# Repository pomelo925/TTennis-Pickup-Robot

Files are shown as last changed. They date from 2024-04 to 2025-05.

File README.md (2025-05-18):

<div align="center">
 <h1> TTennis Pickup Robot 桌球自動拾取智慧機器人 </h1>
</div>

> 清華大學 動力機械系25級 畢業專題（2024）

> 本人（pomelo925）負責項目為全軟體、部分韌體及部分電路。
> 非本人負責項目最終會清楚標註貢獻者。

TTennis Pickup Robot 目標是在任意的桌球場中，自動化完成拾取，並抬升內置球架供運動員使用或將桌球傾倒於球架中，使選手能專注於訓練本身。TTennis Pickup Robot 具備動態避障能力，同時用戶可透過遙控器或螢幕來操控機器人，並調整機器人運動參數。

TTennis Pickup Robot 從機構設計、電路板設計、單晶片調適至上層的視覺處理、AI 模型部署、建圖定位與導航避障系統等皆是我們針對特殊的應用場景做開發，並不直接使用市面上的套件。同時軟韌體算法全部開源，代碼已解藕封裝，所有運行節點以虛擬化容器形式運行，十分利於有程式背景的人對特定算法做二次開發。

<br/>


<center>
<p> 以 Nextjs / Framer Motion / Tailwind CSS 製作的 Web 操控介面。 <p>
</center>

</br>

<div align="center">
 <h2> ⭐⭐⭐ 整體架構 ⭐⭐⭐</h2>
</div>

如下圖，本專題主要區分為以下四大部分。

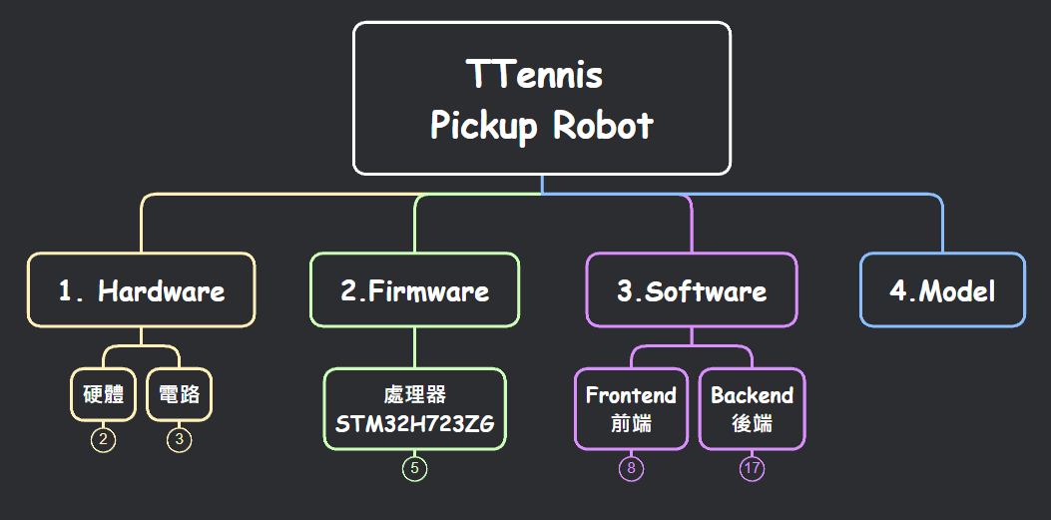
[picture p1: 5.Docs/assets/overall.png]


</br>

<div align="center">
 <h2> ⭐⭐ Hardware 硬體 ⭐⭐</h2>
</div>

外購硬體主要有相機 [Intel® RealSense™ Depth Camera D435](https://www.intelrealsense.com/depth-camera-d435/)、[Luxonis OAK-D](https://shop.luxonis.com/products/oak-d?srsltid=AfmBOoonQ7t1-zn0nqSzjS6hqH9pHZsBbMcbB3aGryrPGHOZsLWWNm30) 以及上位機 [iKOOLCORE R2](https://www.ikoolcore.com/en-tw/products/ikoolcore-r2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)。

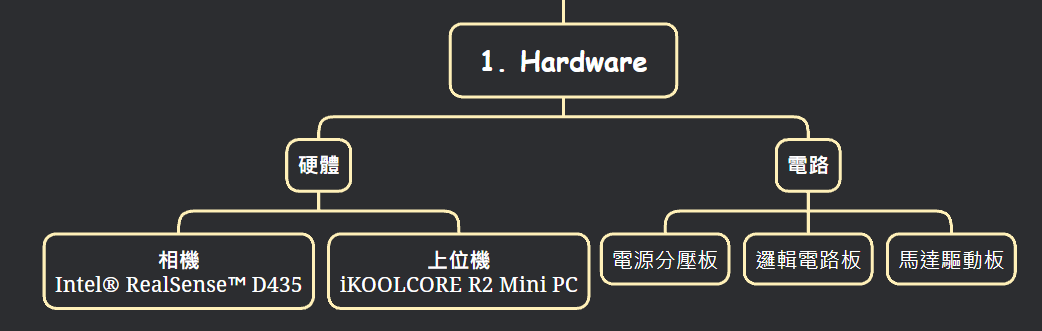
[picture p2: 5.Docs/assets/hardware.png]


我們自行設計 PCB 以增加複雜電路的穩定性與減少過多明線帶來的困擾。包含以下三塊電路板：

* 電源分壓板：將 [18V工具機鋰電池](https://www.makitatools.com/products/details/BL1850B-2) 降壓至12V、5V、3.3V，同時支援 PD 快充，並且防電源反接及短路保護。其中 DC-DC Bucker 皆採用可調式閉路電壓控制晶片，並充分考慮降噪濾波。PD 快充用以支援上位機的運作。

* 邏輯電路板：運算單元為 Cortex M7 內核的 [STM32H723ZGT6](https://www.mouser.tw/ProductDetail/STMicroelectronics/STM32H723ZGT6?qs=sPbYRqrBIVkPaOxQT7wG%252BA%3D%3D)，包含讀取直流馬達之增量式編碼器、閉路控制直流馬達、ROS1 節點通訊等等。並引出 USART 通訊引腳、編碼器端子座、外部晶振時間源、CP2102 TTL 轉 Type-C 通訊等等。

* 馬達驅動板：電力直接由電源分壓板供給 12V，PWM 控制訊號則由邏輯電路板經軟排線傳遞，馬達驅動晶片為 [VNH5019](https://www.mouser.tw/ProductDetail/STMicroelectronics/EVAL-VNH5019-P1?qs=4b8myOmUP%252BuULWYKW0CsPg%3D%3D)。由於功率較大，與邏輯電路板做物理隔離，抗 EMI。 



</br></br>

<div align="center">
    <h2>⭐⭐ Firmware 韌體 ⭐⭐</h2>
</div>

開發平台為 [STM32CubeIDE](https://www.st.com/en/development-tools/stm32cubeide.html)，下圖為本專案資料夾架構與各自任務。

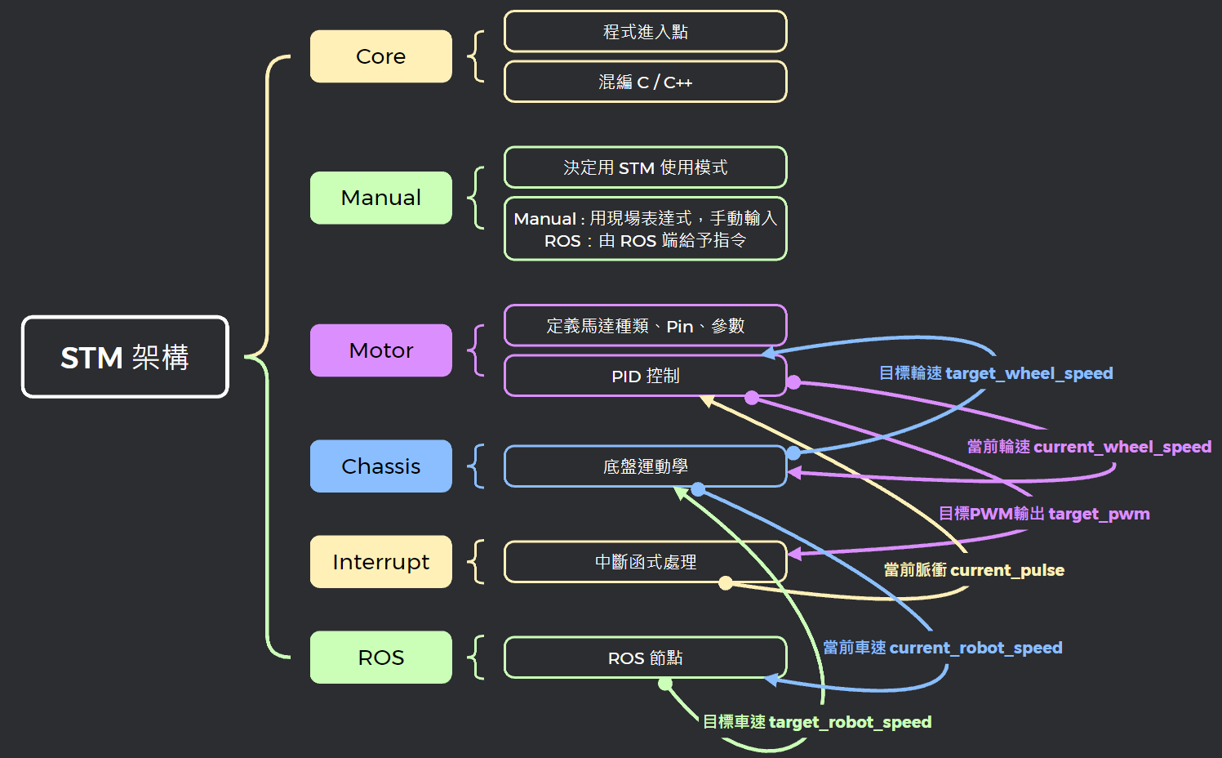
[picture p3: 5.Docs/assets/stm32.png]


此為 C/C++ 混編專案，並將代碼封裝成以任務為導向的獨立資料夾，解藕並增加可移植性，架構圖中的箭頭部分，是針對底盤馬達PID調適中，ROS1、STM32、timer 間的變數傳遞關係。

> 實作細節可參閱 [全端機器人技術筆記 -【韌體】STM32CubeIDE - C/C++ 混編專案架構](https://hackmd.io/@925/robot/%2F%40925%2Fstm-project)。

</br></br>

<div align="center">
 <h2> ⭐⭐ Software 軟體 ⭐⭐ </h2>
</div>

軟體複雜度較高，因此會拆分成較多部分說明。

所有軟體的節點皆以 x86 arch Docker 容器形式啟動與結束，容器間共享網路與記憶體。

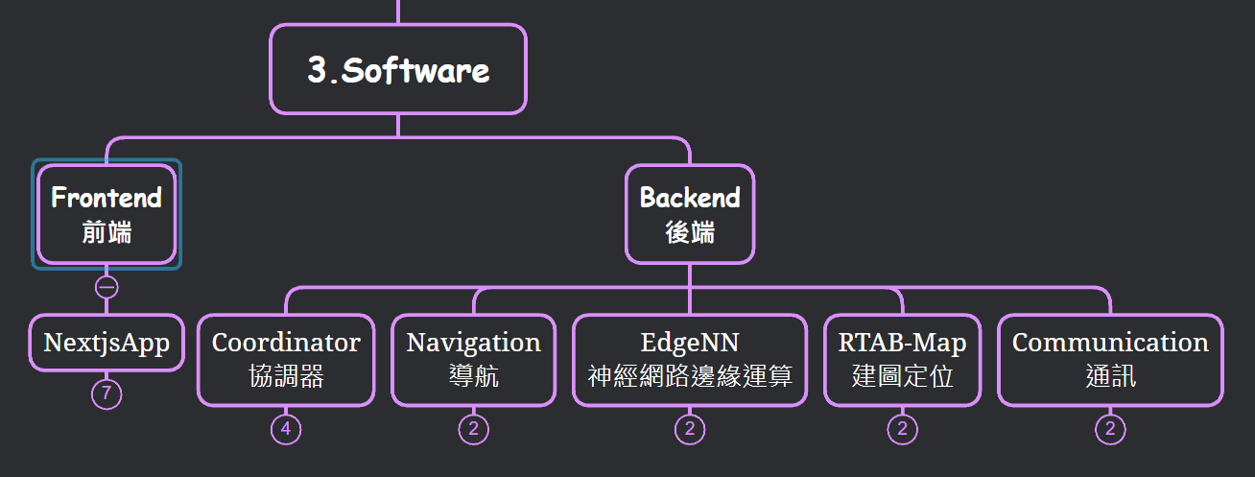
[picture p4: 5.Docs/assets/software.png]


這裡簡述各區塊任務，並於底下補述細節。後端軟體幾乎運行於 [ROS2](https://docs.ros.org/en/foxy/index.html) 平台之上。開發工具主要使用 [Visual Studio Code](https://code.visualstudio.com/)、[Cursor](https://www.cursor.com/)、[MobaXTerm](https://mobaxterm.mobatek.net/) 及 [Foxglove](https://foxglove.dev/ros) 等。

* 前端 - Nextjs / Framer Motion / Tailwind CSS
  * 與用戶最直接的交互接口，可點擊螢幕使機器人執行任務，亦顯示機器人即時運動訊息。
  * 本專案模板與架構很大程度地參考 [
Cristian Mihai 的開源專案](https://www.youtube.com/watch?v=dImgZ_AH7uA&t=194s)。

* 後端 - Coordinator 協調器
  * 作為最上層的節點排程與協調器，依當前任務及情景動態調度必要資源。

* 後端 - Navigation 導航
  * 基於官方開源 [Nav2 導航堆棧](https://docs.nav2.org/)，開發 AMR 的路徑規劃、動靜態避障、代價地圖堆疊等。

* 後端 - EdgeNN 神經網路邊緣運算
  * [Luxonis OAK-D](https://shop.luxonis.com/products/oak-d?srsltid=AfmBOoonQ7t1-zn0nqSzjS6hqH9pHZsBbMcbB3aGryrPGHOZsLWWNm30)，即時偵測桌球、桌球桌、置球架以及運動員，並回傳空間座標資訊。

* 後端 - RTAB-Map 建圖定位
  * 使用開源 [RTAB-Map](https://introlab.github.io/rtabmap/) 為室內環境作三維建模，為導航節點提供定位的依據。

* 後端 - Coomunication 通訊
  * 基於 [rosserial](https://wiki.ros.org/rosserial) 實現 STM - ROS1 通訊。
  * 基於 [ROS1 Bridge](https://github.com/ros2/ros1_bridge) 實現 ROS1 - ROS2 通訊。

</br></br>

<div align="center">
 <h2> ⭐ 軟體前端 - Nextjs x Framer Motion⭐ </h2>
</div>

介面 DEMO 示例，僅：


</br></br>

<div align="center">
 <h2> ⭐ 軟體後端 - EdgeNN ⭐ </h2>
</div>

機上搭載嵌入式 AI RGBD 相機 [Luxonis OAK-D](https://shop.luxonis.com/products/oak-d?srsltid=AfmBOoonQ7t1-zn0nqSzjS6hqH9pHZsBbMcbB3aGryrPGHOZsLWWNm30)，大大減少了上位機的運算負擔。相機端給出偵測物件的空間座標資訊後，經過靜態與動態的座標轉換（基於 [tf2](https://docs.ros.org/en/foxy/Tutorials/Intermediate/Tf2/Tf2-Main.html)）後映射至導航的全局代價地圖中。

本專案使用模型為 [Ultralytics](https://www.ultralytics.com/zh) 發佈的 [YOLOv8 模型](https://github.com/ultralytics/ultralytics)。此為當前 [depthai-experiments
](https://github.com/luxonis/depthai-experiments) 能支援 [on-device programming](https://docs-old.luxonis.com/en/latest/pages/tutorials/on-device-programming/) 的最新模型。部署時須將 yolov8n 模型變體之權重檔轉為輕量化格式，實測幀率浮動於 6 ~ 10 hz 間。

training set 主要由 [Roboflow Universe](https://universe.roboflow.com/) 上已 annotated 的開源資料集 [Ping Pong Detection Computer Vision Project](https://universe.roboflow.com/pingpong-ojuhj/ping-pong-detection-0guzq) 提供。資料再由 [Roboflow](https://roboflow.com/) 協助增強處理，並於本地端（RTX 4070、32GB RAM）滿載訓練。

> 訓練細節可參考 [機器人全端技術筆記 -【軟體】影像處理 -【物件偵測】Training 階段](https://hackmd.io/@925/robot/%2F%40925%2Ftraining)。

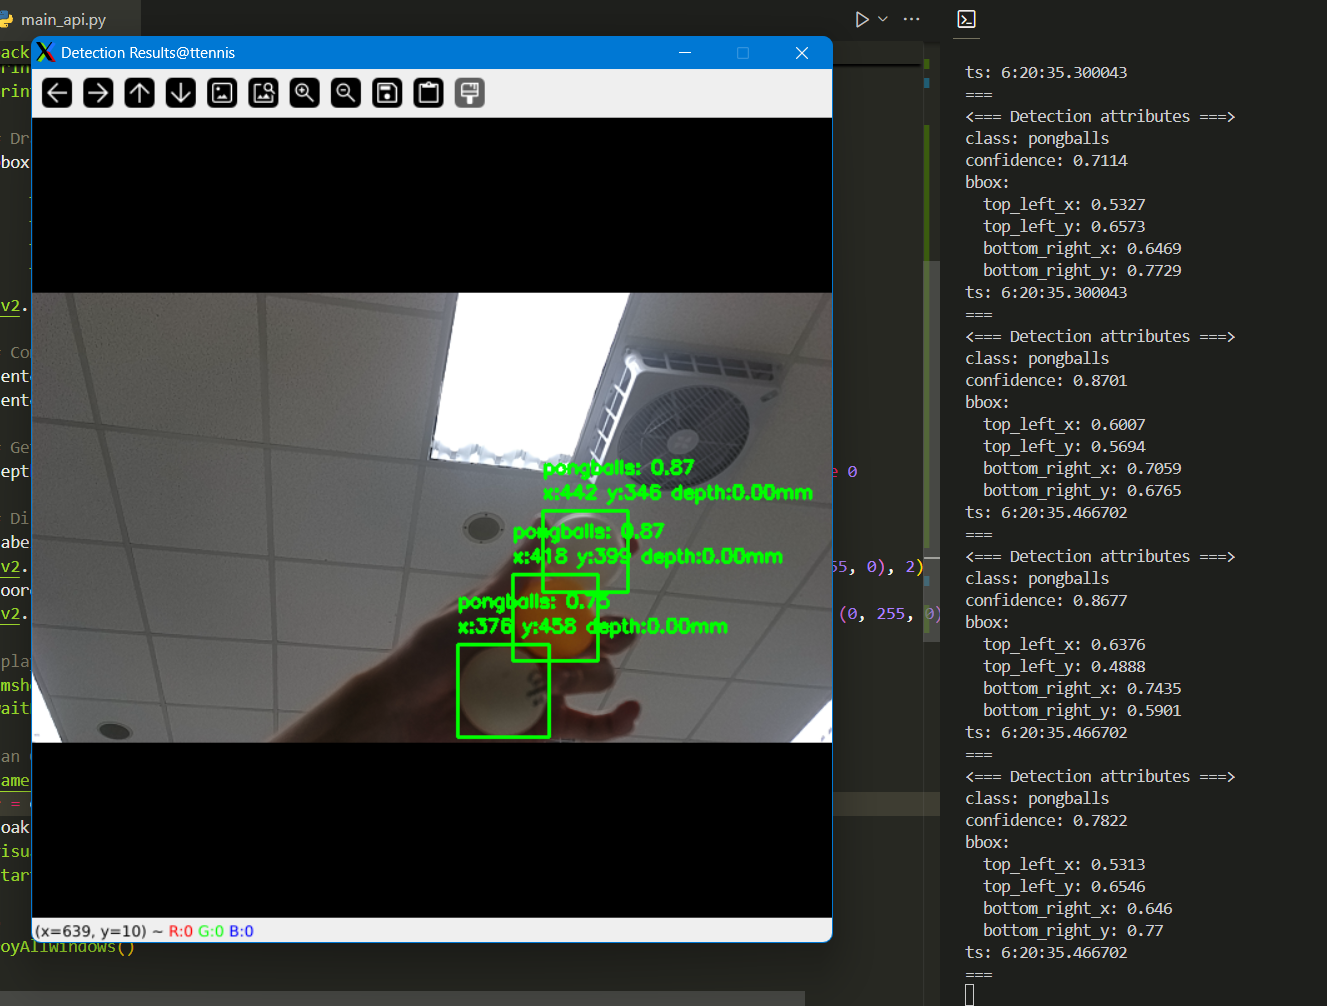
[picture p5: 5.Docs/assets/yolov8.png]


最後，為了取得深度資訊，須使用 DepthAI 的 [YoloSpatialDetectionNetwork](https://docs.luxonis.com/software/depthai-components/nodes/yolo_spatial_detection_network/)，疊合相機原生深度資訊與 YOLO 物件屬性，計算出偵測物件合理的空間座標。

> 此部分詳情可參閱 [機器人全端技術筆記 -【軟體】影像處理 -【物件偵測】Deploying 階段](https://hackmd.io/@925/robot/%2F%40925%2Fdeploy)。

</br></br>

<div align="center">
 <h2> ⭐ 軟體後端 - RTAB-Map ⭐ </h2>
</div>

使用 [RTAB-Map](https://introlab.github.io/rtabmap/) 的主因為歷史悠久、有即時性需求且支援 ROS2（[rtabmap_ros](https://github.com/introlab/rtabmap_ros)），視覺來源為提供 RGBD 資訊的 [Intel® RealSense™ Depth Camera D435](https://www.intelrealsense.com/depth-camera-d435/)、視覺里程計以及底盤從動輪的里程計資訊，並做 EKF 融合。

建圖定位狀況可由 [foxglove](https://foxglove.dev/ros) real-time 觀察，遠端時的效果比 ROS 原生的 [RViz](https://wiki.ros.org/rviz) 和 [Gazebo](https://gazebosim.org/home) 順暢許多。此外所有程序的 [foxglove bridge port](https://docs.foxglove.dev/docs/connecting-to-data/ros-foxglove-bridge/) 皆錯開，避免端口阻塞。

</br></br>

<div align="center">
 <h2> ⭐ 軟體後端 - Communication ⭐ </h2>
</div>

通訊節點如上所述，執行任務明確有二，「STM32 - ROS1 通訊」與「ROS1 - ROS2 通訊」。其實合理的架構是將 [microros](https://micro.ros.org/) 部署於 STM32 上，但礙於諸多測試錯誤且時間不夠。 

關於 STM32 - ROS1 通訊，
> STM32 - ROS1 通訊可參閱 [機器人全端技術筆記 -【韌體】STM32CubeIDE - STM x ROS1](https://hackmd.io/@925/robot/%2F%40925%2Fstmros)。

</br>

關於 ROS1 - ROS2 通訊，十分感謝電資系朋友將 ROS2 Humble 版本的 ROS1 bridge 通訊之 Dockerfile 盡可能地做了容量優化，省下不少開發時間。這裡附上 Github：[YuZhong-Chen/ros2-essentials](https://github.com/YuZhong-Chen/ros2-essentials)、[j3soon/ros2-essentials](https://github.com/j3soon/ros2-essentials)。

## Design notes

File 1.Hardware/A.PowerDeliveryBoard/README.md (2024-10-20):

# Power Delivery Board 大電流降壓電路模塊

本專案為嘉立創之 EasyEDA 上設計，其轉檔生出的 Altium Designer 檔案可能會有些許跑版。
雙層板設計，SMT 貼片及電路板印刷一條龍服務，平均單片 1500 NTD 左右。

## 雷區

犯了兩個很蠢的錯誤：

1. 5V Type-C 口封裝 lay 反。
2. 12V 及 5V 的功率電感封裝尺寸畫錯，實際大上近乎兩倍。 

其餘主要功能正常，該注意也有注意，細項如下。

## 需求與功能

1. Vin：18~25V；Vout：100W PD/12V/5V。
2. 穩定承載 30A 電流。
3. PD/QC 晶片為 Buck-Boost 電路，~12V/5V 為 Buck 電路。
4. 皆採外置同步 NMOS 驅動大電流。
5. 12V 需承載最大電流，外置 NMOS 採雙並聯以拉高承載電流。
6. 具 PMOS 防反接，LED 通電指示燈。

## 設計注意事項

1. ~12V/5V 功率電感採鐵硅鋁電感為最佳解。
2. 鐵硅鋁電感，半屏蔽或無屏蔽，其下方不可鋪銅避免 EMI。
3. 大面積鋪銅，提高電流承載。
4. 打大量 via 提升散熱效率。
5. 同步整流之功率迴路須盡可能地小，本專案採 U 型佈局。

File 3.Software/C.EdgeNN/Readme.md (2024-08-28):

# EdgeNN

EdgeNN is an edge AI framework designed to provide efficient and low-latency AI computing capabilities for edge devices.

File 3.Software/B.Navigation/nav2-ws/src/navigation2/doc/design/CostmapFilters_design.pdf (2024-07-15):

# Costmap Filters High-Level Design

v.1.1

## ROS2 Overall Structure

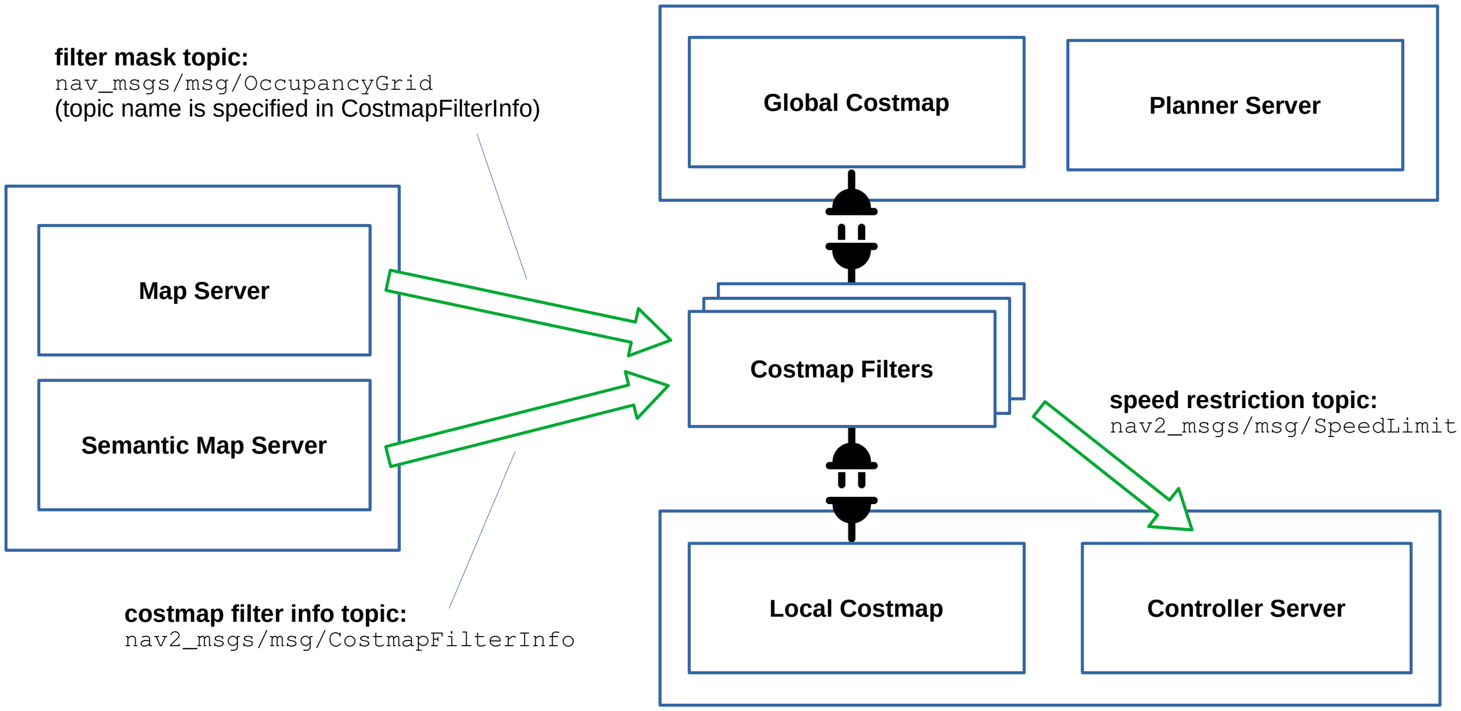
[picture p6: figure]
Controller Server; filter mask topic: nav_msgs/msg/OccupancyGrid; Local Costmap; Global Costmap; Planner Server; speed restriction topic: nav2_msgs/msg/SpeedLimit; Map Server; Semantic Map Server; costmap filter info topic: nav2_msgs/msg/CostmapFilterInfo

(topic name is specified in CostmapFilterInfo)

Costmap Filters Costmap Filters Costmap Filters

CostmapLayer

KeepoutFilter
loadFilter() - Creates a subscription to filter_info and filter_mask topics.

process() - Based on loaded map composes Costmap2D with
[FREE_SPACE..LETHAL_OBSTACLE] cost depending on data value in filter_mask.

SpeedFilter
loadFilter() - Creates a subscription to filter_info and filter_mask topics. Creates a publisher for speed_limit topic.

process() - Checks whether the robot is entered or leaved marked on map speed restriction area. If entered checks the speed limit and sets speed_limit topic value. If leaved restores back speed_limit topic value to no-limit.

LanesFilter
Covered by KeepoutFilter (#1522). (https://github.com/ros-planning/navigation2/issues/1522)

CostmapFilter
class CostmapFilter {
public:
virtual initializeFilter(
const std::string & filter_info_topic) = 0; virtual process(
Costmap2D & master_grid, int window_bounds, Pose2D & robot_pose) = 0;
virtual resetFilter() = 0;

protected:
pose last_robot_pose;
};

CostmapFilter::activate() {
// Creates subscriptions to info and mask topics initializeFilter(filter_info_topic);
}

CostmapFilter::deactivate() {
// Reset all subscriptions resetFilter(filter_info_topic); }

CostmapFilter::reset() {
// Reloads filter
resetFilter();
initializeFilter(filter_info_topic);
}

CostmapFilter::updateBounds(robot_pose, bounds) { ...
last_robot_pose = robot_pose;
}

CostmapFilter::updateCosts(
Costmap2D & master_grid, int window_bounds) { ...
// An algorithm for how to use that map's
// information. Fills the Costmap2D with
// calculated data and makes an action based
// on processed data.
process(master_grid, window_bounds, last_robot_pose); }

## Costmap Filters Structure

class
inheritance

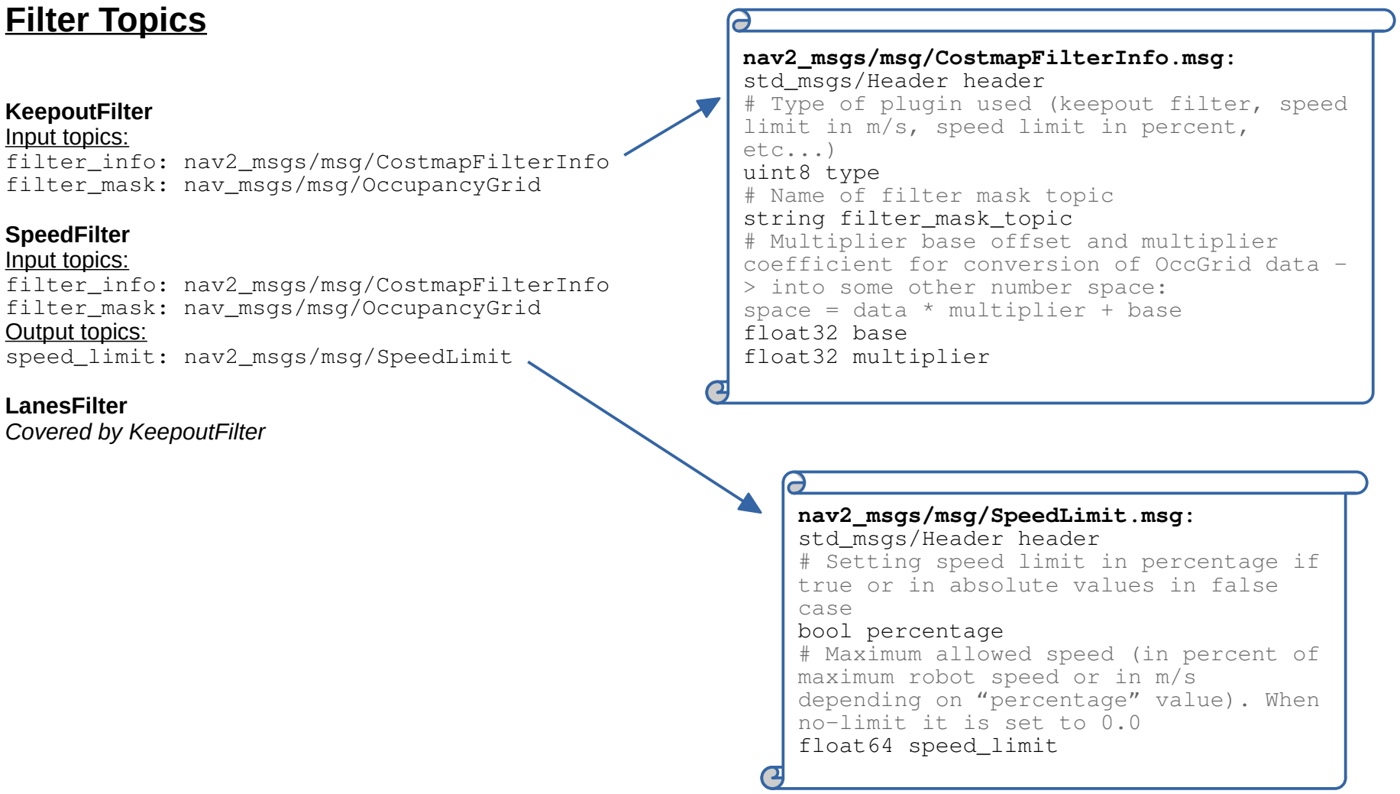
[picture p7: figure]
KeepoutFilter Input topics: filter_info: nav2_msgs/msg/CostmapFilterInfo filter_mask: nav_msgs/msg/OccupancyGrid; SpeedFilter Input topics: filter_info: nav2_msgs/msg/CostmapFilterInfo filter_mask: nav_msgs/msg/OccupancyGrid Output topics: speed_limit: nav2_msgs/msg/SpeedLimit; LanesFilter Covered by KeepoutFilter; Filter Topics; nav2_msgs/msg/CostmapFilterInfo.msg: std_msgs/Header header; limit in m/s, speed limit in percent, etc...) uint8 type # Name of filter mask topic string filter_mask_topic # Multiplier base offset and multiplier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

# Type of plugin used (keepout filter, speed

coefficient for conversion of OccGrid data -

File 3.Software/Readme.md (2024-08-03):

## 3.Software

> 軟體層，本專案分為以下子架構，並皆以獨立容器運行。

以下簡稱四種模式 Maping Mode (MM), Fetching Mode (FM), Serving Mode (SM), Pouring Mode (PM)。

---

### A. Coordinator 協調器

> 主要估能整合多個節點資訊，並發送目標航點給導航。
> 同時為各節點排程。

* **節點排程**：依據不同模式，調用不同節點及參數。

* **最優取球策略**：（僅 FM）由 EdgeNN 資料計算桌球密度、位置、速度等參數，決定最快取球策略。

* **最優探索路徑**：（僅 MM）由 EdgeNN 資料及探索演算法，生成快速探索全地圖的方式。

* **航點發送**：（MM、FM）經計算後，發送目標航點給導航節點。

※ 註：MM、FM 由 coordinator 決定航點；SM, PM 則由使用者透過 UI 決定航點。

---

### B. Navigation 導航

> 自動化的核心，盡可能最快且安全地到達指定點。

* **路徑規劃**：接收外部給予之任務目標點（FM, SM, PM），規劃出最佳路徑。

* **避障**：不同模式的避障邏輯不同。
  * MM：接近任何障礙（理應為靜態），立即停止並轉向新目標點。
  * FM：動態避障，彈性度高且等待時間低，超時將規劃新路徑。
  * SM, PM：靜態避障，將等待障礙離去才會繼續前行。
 
---

### C. EdgeNN

> 處理 Luxonis OAK-D 相機之嵌入式 AI 模型，及 ROS2 接口。

* 自定義訓練集：對人、桌球、桌球桌、球籃做物件偵測。

* ROS2 接口：將物件資訊推送至 ROS2 Topic 之上。

---

### D. RTABMAP

> 處理 RGBD 相機的點雲資訊，用以同時建圖與定位。

* 建圖：（MM）。

* 定位：（FM, SM, PM）。

---

### E. Integration

> 溝通與整合節點，具體來說為以下兩者。

* STM32 與 ROS 1 溝通：透過 rosserial 包搭建韌體端與軟體端之通訊橋梁。

* ROS1 與 ROS2 溝通：透過官方 ROS1 Bridge 包搭建 ROS1 與 ROS2 的通訊。

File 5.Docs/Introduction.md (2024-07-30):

# TTennis Pickup Robot 桌球自動拾取智慧機器人
> 2024年清華大學25級動力機械系畢業專題

> 本人負責項目為所有軟體、部分韌體及部分硬體，其餘非本人負責項目最終會清楚標註貢獻者。

## 摘要
本計畫旨在研發一台可以自動撿桌球且將桌球放入發球機的機器人，以減輕桌球運動員的負擔，並提高其訓練的效率。綜合評估了幾款現有自動撿球機器人的優缺點後，我們確立研究的主要目標為提升現有自動撿球機器人的功能，包括提高取球效率、增加集球倉容量、引入自動辨識球和動態避障功能等。具體研究方法為透過機器人的差動底盤、取球機構，以及深度相機的RGBD資訊、ROS(Robot Operating System)系統、Wi-Fi通訊等，達成此機器人能夠高效、快速地自動收集桌球，且提供建圖定位、撿球模式、供球模式和倒球模式等多元模式，且有利於使用者簡易操作的設備，從而提高運動員訓練的效率。

## 研究動機與研究問題
在桌球運動中，無論是業餘對打或專業訓練，球員經常須花費大量時間和精力在場上撿球，此單調而繁瑣的事情卻佔據一大部分的運動時間。尤其對於專業運動員，長時間反覆性的彎腰撿球不僅浪費訓練時間，也可能造成腰部疲勞或肌肉損傷。

鑒於以上，我們想研發一台智慧自動桌球拾取機器人，代替球員雙手拾球，使運動員能夠更有效率地訓練，而業餘者也能省免撿球麻煩而享受對打樂趣。此機器人主要用於一般性的娛樂或訓練場地等，自動尋找並拾取場上大數量的桌球，並將球供給球員。由於正式專業的桌球比賽上，為了確保賽場內無干擾物，球場上只允許有一顆桌球，按照慣例球員須自行撿球。此場景中機器人反而會影響球賽，因此我們設計的拾取機器人並不會用於正式比賽上。

基於上述動機，我們需要考量以下問題：
1. 自動撿桌球機器人的設計：我們須要設計一個能夠自主辨識、撿取和歸還球的機器人系統。這需要結合機器視覺、機器人控制、感知技術等多個領域的知識和技術，以確保機器人能夠正確地辨識並準確地撿取和歸還球。
2. 效率和速度：自動撿桌球機器人的效率和速度對於其實用性至關重要。機器人的機構設計須最大程度地提高撿球效率，並且確保它在訓練場地中的操作速度足夠快，以滿足運動員的需求。
3. 動態避障：拾取機器人會在桌球場上快速移動，如何在機器人執行任務的同時避開運動員也非常重要，若因避障影響撿球效率是可預期而難以避免的，然我們仍會思考如何更有效率地規劃避障演算法。

## 研究方法及步驟
### 1. 機構設計
機構目標是高效率地蒐集場上桌球，並能在機器內儲存至少200顆。初步的機構規劃可分為以下四個部分：

  * 差動底盤：負責機器的移動
        差動底盤使用前方左右各一的膠輪作為主動輪，後方的兩顆萬向輪作為從動輪。這樣的配置讓機器能精確且快速地移動和轉向，同時後方的萬向輪在不影響機器轉向的前提下，能有效避免車體傾倒。另外，為了防止機器在移動過程中因地面不平整而打滑，作為主動輪的膠輪會採取懸吊的設計，使用彈簧進行避震。
  
  * intake機構：轉動滾筒蒐集地上桌球
    負責蒐集場上桌球的 Intake 機構是機器人比賽中經常使用的設計，從文獻回顧的地方也可以看到不少現有機種也有使用，其特點是能夠快速地收集重量較輕的物體，非常適合本次計畫收集桌球的任務。我們計劃在機器的前端安裝三個較長的滾筒，這些滾筒由一顆直流馬達驅動，通過皮帶連接，使得它們能夠同時高速旋轉。當這些滾筒旋轉時，會一次性將多顆機器前方散落的桌球掃入機器體內，相較於現有機種intake只能一次捲入一顆，我們設計的機構能夠實現更快速且有效的蒐集任務。
  
  * 環形輸送帶：將桌球運送至集球倉
    當桌球收集至機器體內後，我們會使用一個垂直的環形輸送帶來抬升這些桌球，靈感來源於水車。實現方式是在輸送帶上安裝許多籃子，使其沿著軌道循環，這些籃子會將桌球從機器體內抬升，然後將它們從集球倉的頂部落入集球倉中。這樣的設計可以將桌球穩定且快速地儲存到集球倉中，使得機器能夠持續進行蒐集任務。
  
  * 升降集球倉：用於儲存桌球。
    桌球經由前面的流程落入集球倉內，基於一般桌球置球架的容量大概在200顆左右，所以我們訂定集球倉的預計容量也要達到至少200顆。同時，為了方便運動員取球，集球倉會具有抬升功能，當運動員需要使用時，集球倉將抬升至一個方便取球的高度。抬升的機構預計採取繩排伸縮，使用馬達將線材捲起，透過安裝在滑軌上的滑輪將整個集球倉拉起至足夠的高度，使運動員可以不用彎腰，直接伸手從集球倉拿取乒乓球。此外，有時運動員會用發球機進行訓練，因此集球倉的一側會由伺服馬達控制擋板，當集球倉抬升至發球機的高度時，擋板會放下，使得桌球因集球倉底部的傾斜而滾入發球機內，實現更加多樣化的功能。

### 2. 軟體架構
   
  軟體端部分，首先機器人藉由深度相機獲取RGBD資訊，利用Ultralytics YOLOv8對RGB影像推論桌球相對於機身的位置，並透過座標轉換取得桌球與我機中心之位置。影像系統將資訊發佈給主程式後，交由其規劃目標點並發佈目標點給導航系統，導航會規劃到達目標點的行走路徑，包含最短路徑與動靜態避障之間的權衡，最後發佈底盤移動速度給STM微晶片控制板，並驅動無刷及直流馬達。

  導航系統除了避障，另一部份是使用RGBD-SLAM建圖技術實現機器室內定位。這一切的軟體將交由上位機負責計算，我們採用能夠應對即時神經網絡辨識大量計算的Intel Alder Lake N95/i3-N300 iKOOLCORE R2 N300，它提供足夠的USB 3.2接口並支持4K@60fps的影像傳輸，並有被動冷卻設計，確保電腦能長時間在封閉的機器內部穩定運行而不熱當。

  接著是定位系統，考慮到SLAM建圖技術有即時計算需求，將採用RTAB-map作為基礎開發，透過對較少被訪問到的地圖點放入LTM(Long-Term Memory)中以減少運算量；而導航系統，則使用典型的navigation stack導航架構，move_base庫以gmapping整合定位建圖資訊並存入靜態地圖，爾後透過對我機及動靜態障礙物設立膨脹層以形成costmap，規劃與目標點之最佳全局與區域路徑。最後，主程式負責接收遙控器指令，並在行走時整合所有資訊，作為各系統間的溝通橋樑。

  軟體端開發環境上，我們選擇開發社群廣大且技術成熟的ROS(Robot Operating System)，其豐富開源的軟體包可滿足本次計畫需求。影像處理系統，將透過訂閱由realsense-ros發佈的訊息，使用ROS的PCL庫稀疏化影像(VoxelGrid Filter)，並配合DBSCAN聚類演算法分割不同物體之邊緣。

  ROS開發過程中，可搭配其內建視覺化工具Rviz及Gazebo，協助開發經過濾後的遮罩影像，和觀察機器人在模擬環境中的避障表現，盡量降低實機測試之風險。另外，機器人的軟體開發皆將基於docker虛擬化技術之上，所開發之應用程序也將以容器形式啟動，目的是提升程序的便攜性，若未來機器有量產需求，可輕易移植於其他相同硬體架構之主機上。

### 3. 感測器、韌體以及通訊：
感測器與軔體(圖八中的淺橘色區塊)部分，機器人須配備廣角相機以盡可能地捕獲場地上乒乓球和運動員的動態資訊。由於有YOLO深度學習和RGBD SLAM的建圖需求，相機必須同時獲取RGB8和深度資訊，我們研究後選擇Intel® RealSense™ depth camera D435，其自身搭載Vision Processor D4計算單元，能減輕上位機計算負擔，同時可使用官方開源Intel® RealSense™ SDK 2.0，增強開發靈活性與適應性。

另一方面，在韌體計算單元上，我們選擇基於ARM架構的STM32H723ZG微晶片，以滿足對多個直流馬達的速度控制和timer設定需求。同時，它也支援SPI、I2C、ETH及USART等多種通訊協議，其中UART協議將作為rosserial通訊接口基礎，作為STM端和上位機ROS端溝通橋梁。在開發上將使用STM32CubeIDE撰寫與燒錄韌體程式碼。

最後是遙控觸控螢幕，會安裝有Wi-Fi模組的ESP32，用於與機器人溝通。ESP32會接收螢幕按鈕上的觸控指令，並透過Wi-Fi發佈控制訊息給機器人。

## 預期結果
考慮到智慧自動桌球機器人的實用性及商品化，以下場景為使用者首次使用此機器人時，應有的預期操作模式與結果。
* 安裝桌邊遙控器：使用者可根據操作手冊安裝遙控器於桌球桌邊。
* 開機：透過遙控器喚醒機器人。
* 建圖定位：機器人須對新環境探索並做建圖，作為日後行走之地圖依據。此時使用者須清空場地不必要阻礙物。使用者點擊「探索環境」後，機器人便進入建圖模式，測試相機與底盤馬達運作正常後，開始根據演算法隨機探索地圖並生成靜態地圖。當所有環境皆存入後，機器會回到原點，並顯示「探索結束」。此步驟只須執行一次。
* 撿球模式：此模式須確保已執行過建圖定位。機器人在撿球模式中，機器人將在桌球場中尋找並蒐集桌球，使用者可調整機器人移動速度。機器人會持續在場上尋找與蒐集(即便沒有桌球)，直至即將沒電、使用者呼叫、異物阻塞等情況機器人才會停止撿球。
* 呼叫按鈕：使用者可隨時點擊觸控螢幕上的「呼叫」按鈕，機器人會立即停止當前工作，並移動至原點。
* 供球模式：機器人將移動到球員身旁並佇立於原地，抬起集球箱供給球員進行發球練習。使用者可透過螢幕微調機器人的位置。
* 倒球模式：或稱發球機模式。此模式會先確認使用者是否已安裝桌球發球機，或是否已在對面球桌安裝集球網。機器人會移動至合適位置，抬起集球箱後打開箱上之閘門，使球落入集球網中，供給桌球給發球機。

關於機器人在撿球表現上的預期細節，首先移動速度最高可至一米/秒，路徑上之桌球都能順利吸入機器內部，且整體運作聲音小於環境噪聲。集球倉預計至少可儲存200顆桌球，且不管何種位置或角度吸入桌球，機內之桌球流水線皆不會受到干涉。避障部分，若是於首次建圖中遇到之障礙物，將列為禁區而永不進入；若是於行進中遇到之新障礙物，將在一定距離時停止行走，並重新規劃新路徑行走。由於避障系統的核心訴求是「不可對使用者造成任何傷害」，因此我們會以安全為最高原則開發，若因避障影響撿球效率是可預期而難以避免的，然我們仍會思考如何更有效率地規劃避障演算法。

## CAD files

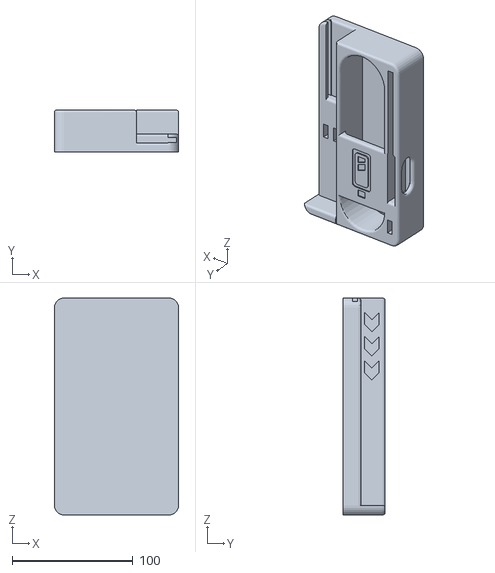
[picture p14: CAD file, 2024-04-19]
4.Model/epomaker_RT100.stl
103.0 x 35.0 x 180.0

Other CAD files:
4.Model/Computer/Jetson TX2/032-0037-000_2.ipt
4.Model/Computer/Jetson TX2/032-0056-000_2.ipt
4.Model/Computer/Jetson TX2/032-0131-000_2.ipt
4.Model/Computer/Jetson TX2/032-0153-000_2.ipt
4.Model/Computer/Jetson TX2/032-0166-000_3.ipt
4.Model/Computer/Jetson TX2/032-0186-000_1.ipt
4.Model/Computer/Jetson TX2/032-0195-000_1.ipt
4.Model/Computer/Jetson TX2/032-0204-000_2.ipt
4.Model/Computer/Jetson TX2/032-0213-000_1.ipt
4.Model/Computer/Jetson TX2/032-0240-000_2.ipt
4.Model/Computer/Jetson TX2/032-0335-000_1.ipt
4.Model/Computer/Jetson TX2/032-0421-000_2.ipt
4.Model/Computer/Jetson TX2/032-0421-000_3.ipt
4.Model/Computer/Jetson TX2/032-0468-000_1.ipt
4.Model/Computer/Jetson TX2/032-0470-000_2.ipt
4.Model/Computer/Jetson TX2/032-0471-000_2.ipt
4.Model/Computer/Jetson TX2/032-0627-000_1.ipt
4.Model/Computer/Jetson TX2/032-0628-000_1.ipt
4.Model/Computer/Jetson TX2/032-0636-000_1.ipt
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

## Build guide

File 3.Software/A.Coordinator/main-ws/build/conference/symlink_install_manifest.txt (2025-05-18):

/home/main-ws/install/conference/lib/conference/libnav.a
/home/main-ws/install/conference/lib/conference/libintake.a
/home/main-ws/install/conference/lib/conference/libelevator.a
/home/main-ws/install/conference/lib/conference/libbasket.a
/home/main-ws/install/conference/lib/conference/demo_nav_retrieval
/home/main-ws/install/conference/lib/conference/demo_retrieval_drop
/home/main-ws/install/conference/lib/conference/demo_retrieval_supply
/home/main-ws/install/conference/lib/conference/demo_intake
/home/main-ws/install/conference/lib/conference/demo_elevator
/home/main-ws/install/conference/share/ament_index/resource_index/package_run_dependencies/conference
/home/main-ws/install/conference/share/ament_index/resource_index/parent_prefix_path/conference
/home/main-ws/install/conference/share/conference/environment/ament_prefix_path.sh
/home/main-ws/install/conference/share/conference/environment/ament_prefix_path.dsv
/home/main-ws/install/conference/share/conference/environment/path.sh
/home/main-ws/install/conference/share/conference/environment/path.dsv
/home/main-ws/install/conference/share/conference/local_setup.bash
/home/main-ws/install/conference/share/conference/local_setup.sh
/home/main-ws/install/conference/share/conference/local_setup.zsh
/home/main-ws/install/conference/share/conference/local_setup.dsv
/home/main-ws/install/conference/share/conference/package.dsv
/home/main-ws/install/conference/share/ament_index/resource_index/packages/conference
/home/main-ws/install/conference/share/conference/cmake/conferenceConfig.cmake
/home/main-ws/install/conference/share/conference/cmake/conferenceConfig-version.cmake
/home/main-ws/install/conference/share/conference/package.xml

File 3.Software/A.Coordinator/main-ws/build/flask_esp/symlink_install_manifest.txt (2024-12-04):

/home/main-ws/install/flask_esp/lib/flask_esp/scripts/button_press_publisher.py
/home/main-ws/install/flask_esp/share/ament_index/resource_index/package_run_dependencies/flask_esp
/home/main-ws/install/flask_esp/share/ament_index/resource_index/parent_prefix_path/flask_esp
/home/main-ws/install/flask_esp/share/flask_esp/environment/ament_prefix_path.sh
/home/main-ws/install/flask_esp/share/flask_esp/environment/ament_prefix_path.dsv
/home/main-ws/install/flask_esp/share/flask_esp/environment/path.sh
/home/main-ws/install/flask_esp/share/flask_esp/environment/path.dsv
/home/main-ws/install/flask_esp/share/flask_esp/local_setup.bash
/home/main-ws/install/flask_esp/share/flask_esp/local_setup.sh
/home/main-ws/install/flask_esp/share/flask_esp/local_setup.zsh
/home/main-ws/install/flask_esp/share/flask_esp/local_setup.dsv
/home/main-ws/install/flask_esp/share/flask_esp/package.dsv
/home/main-ws/install/flask_esp/share/ament_index/resource_index/packages/flask_esp
/home/main-ws/install/flask_esp/share/flask_esp/cmake/flask_espConfig.cmake
/home/main-ws/install/flask_esp/share/flask_esp/cmake/flask_espConfig-version.cmake
/home/main-ws/install/flask_esp/share/flask_esp/package.xml

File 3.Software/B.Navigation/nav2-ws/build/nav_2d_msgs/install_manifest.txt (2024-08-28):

/home/nav2-ws/install/nav_2d_msgs/lib/libnav_2d_msgs__rosidl_generator_c.so
/home/nav2-ws/install/nav_2d_msgs/lib/libnav_2d_msgs__rosidl_typesupport_fastrtps_c.so
/home/nav2-ws/install/nav_2d_msgs/lib/libnav_2d_msgs__rosidl_typesupport_fastrtps_cpp.so
/home/nav2-ws/install/nav_2d_msgs/lib/libnav_2d_msgs__rosidl_typesupport_introspection_c.so
/home/nav2-ws/install/nav_2d_msgs/lib/libnav_2d_msgs__rosidl_typesupport_c.so
/home/nav2-ws/install/nav_2d_msgs/lib/libnav_2d_msgs__rosidl_typesupport_introspection_cpp.so
/home/nav2-ws/install/nav_2d_msgs/lib/libnav_2d_msgs__rosidl_typesupport_cpp.so
/home/nav2-ws/install/nav_2d_msgs/lib/libnav_2d_msgs__rosidl_generator_py.so
/home/nav2-ws/install/nav_2d_msgs/share/nav_2d_msgs/cmake/export_nav_2d_msgs__rosidl_generator_cExport.cmake
/home/nav2-ws/install/nav_2d_msgs/share/nav_2d_msgs/cmake/export_nav_2d_msgs__rosidl_generator_cExport-noconfig.cmake
/home/nav2-ws/install/nav_2d_msgs/share/nav_2d_msgs/cmake/export_nav_2d_msgs__rosidl_typesupport_fastrtps_cExport.cmake
/home/nav2-ws/install/nav_2d_msgs/share/nav_2d_msgs/cmake/export_nav_2d_msgs__rosidl_typesupport_fastrtps_cExport-noconfig.cmake
/home/nav2-ws/install/nav_2d_msgs/share/nav_2d_msgs/cmake/export_nav_2d_msgs__rosidl_generator_cppExport.cmake
/home/nav2-ws/install/nav_2d_msgs/share/nav_2d_msgs/cmake/export_nav_2d_msgs__rosidl_typesupport_fastrtps_cppExport.cmake
/home/nav2-ws/install/nav_2d_msgs/share/nav_2d_msgs/cmake/export_nav_2d_msgs__rosidl_typesupport_fastrtps_cppExport-noconfig.cmake
/home/nav2-ws/install/nav_2d_msgs/share/nav_2d_msgs/cmake/nav_2d_msgs__rosidl_typesupport_introspection_cExport.cmake
/home/nav2-ws/install/nav_2d_msgs/share/nav_2d_msgs/cmake/nav_2d_msgs__rosidl_typesupport_introspection_cExport-noconfig.cmake
/home/nav2-ws/install/nav_2d_msgs/share/nav_2d_msgs/cmake/nav_2d_msgs__rosidl_typesupport_cExport.cmake
/home/nav2-ws/install/nav_2d_msgs/share/nav_2d_msgs/cmake/nav_2d_msgs__rosidl_typesupport_cExport-noconfig.cmake
/home/nav2-ws/install/nav_2d_msgs/share/nav_2d_msgs/cmake/nav_2d_msgs__rosidl_typesupport_introspection_cppExport.cmake
/home/nav2-ws/install/nav_2d_msgs/share/nav_2d_msgs/cmake/nav_2d_msgs__rosidl_typesupport_introspection_cppExport-noconfig.cmake
/home/nav2-ws/install/nav_2d_msgs/share/nav_2d_msgs/cmake/nav_2d_msgs__rosidl_typesupport_cppExport.cmake
/home/nav2-ws/install/nav_2d_msgs/share/nav_2d_msgs/cmake/nav_2d_msgs__rosidl_typesupport_cppExport-noconfig.cmake
/home/nav2-ws/install/nav_2d_msgs/share/nav_2d_msgs/cmake/export_nav_2d_msgs__rosidl_generator_pyExport.cmake
/home/nav2-ws/install/nav_2d_msgs/share/nav_2d_msgs/cmake/export_nav_2d_msgs__rosidl_generator_pyExport-noconfig.cmake

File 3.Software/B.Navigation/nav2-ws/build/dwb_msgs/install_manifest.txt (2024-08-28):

/home/nav2-ws/install/dwb_msgs/lib/libdwb_msgs__rosidl_generator_c.so
/home/nav2-ws/install/dwb_msgs/lib/libdwb_msgs__rosidl_typesupport_fastrtps_c.so
/home/nav2-ws/install/dwb_msgs/lib/libdwb_msgs__rosidl_typesupport_fastrtps_cpp.so
/home/nav2-ws/install/dwb_msgs/lib/libdwb_msgs__rosidl_typesupport_introspection_c.so
/home/nav2-ws/install/dwb_msgs/lib/libdwb_msgs__rosidl_typesupport_c.so
/home/nav2-ws/install/dwb_msgs/lib/libdwb_msgs__rosidl_typesupport_introspection_cpp.so
/home/nav2-ws/install/dwb_msgs/lib/libdwb_msgs__rosidl_typesupport_cpp.so
/home/nav2-ws/install/dwb_msgs/lib/libdwb_msgs__rosidl_generator_py.so
/home/nav2-ws/install/dwb_msgs/share/dwb_msgs/cmake/export_dwb_msgs__rosidl_generator_cExport.cmake
/home/nav2-ws/install/dwb_msgs/share/dwb_msgs/cmake/export_dwb_msgs__rosidl_generator_cExport-noconfig.cmake
/home/nav2-ws/install/dwb_msgs/share/dwb_msgs/cmake/export_dwb_msgs__rosidl_typesupport_fastrtps_cExport.cmake
/home/nav2-ws/install/dwb_msgs/share/dwb_msgs/cmake/export_dwb_msgs__rosidl_typesupport_fastrtps_cExport-noconfig.cmake
/home/nav2-ws/install/dwb_msgs/share/dwb_msgs/cmake/export_dwb_msgs__rosidl_generator_cppExport.cmake
/home/nav2-ws/install/dwb_msgs/share/dwb_msgs/cmake/export_dwb_msgs__rosidl_typesupport_fastrtps_cppExport.cmake
/home/nav2-ws/install/dwb_msgs/share/dwb_msgs/cmake/export_dwb_msgs__rosidl_typesupport_fastrtps_cppExport-noconfig.cmake
/home/nav2-ws/install/dwb_msgs/share/dwb_msgs/cmake/dwb_msgs__rosidl_typesupport_introspection_cExport.cmake
/home/nav2-ws/install/dwb_msgs/share/dwb_msgs/cmake/dwb_msgs__rosidl_typesupport_introspection_cExport-noconfig.cmake
/home/nav2-ws/install/dwb_msgs/share/dwb_msgs/cmake/dwb_msgs__rosidl_typesupport_cExport.cmake
/home/nav2-ws/install/dwb_msgs/share/dwb_msgs/cmake/dwb_msgs__rosidl_typesupport_cExport-noconfig.cmake
/home/nav2-ws/install/dwb_msgs/share/dwb_msgs/cmake/dwb_msgs__rosidl_typesupport_introspection_cppExport.cmake
/home/nav2-ws/install/dwb_msgs/share/dwb_msgs/cmake/dwb_msgs__rosidl_typesupport_introspection_cppExport-noconfig.cmake
/home/nav2-ws/install/dwb_msgs/share/dwb_msgs/cmake/dwb_msgs__rosidl_typesupport_cppExport.cmake
/home/nav2-ws/install/dwb_msgs/share/dwb_msgs/cmake/dwb_msgs__rosidl_typesupport_cppExport-noconfig.cmake
/home/nav2-ws/install/dwb_msgs/share/dwb_msgs/cmake/export_dwb_msgs__rosidl_generator_pyExport.cmake
/home/nav2-ws/install/dwb_msgs/share/dwb_msgs/cmake/export_dwb_msgs__rosidl_generator_pyExport-noconfig.cmake

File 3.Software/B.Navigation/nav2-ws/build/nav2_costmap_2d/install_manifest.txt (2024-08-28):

/home/nav2-ws/install/nav2_costmap_2d/lib/liblayers.so
/home/nav2-ws/install/nav2_costmap_2d/lib/libfilters.so
/home/nav2-ws/install/nav2_costmap_2d/lib/libnav2_costmap_2d_core.so
/home/nav2-ws/install/nav2_costmap_2d/lib/libnav2_costmap_2d_client.so
/home/nav2-ws/install/nav2_costmap_2d/share/nav2_costmap_2d/cmake/export_nav2_costmap_2dExport.cmake
/home/nav2-ws/install/nav2_costmap_2d/share/nav2_costmap_2d/cmake/export_nav2_costmap_2dExport-release.cmake

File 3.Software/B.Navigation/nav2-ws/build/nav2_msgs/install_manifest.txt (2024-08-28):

/home/nav2-ws/install/nav2_msgs/lib/libnav2_msgs__rosidl_generator_c.so
/home/nav2-ws/install/nav2_msgs/lib/libnav2_msgs__rosidl_typesupport_fastrtps_c.so
/home/nav2-ws/install/nav2_msgs/lib/libnav2_msgs__rosidl_typesupport_fastrtps_cpp.so
/home/nav2-ws/install/nav2_msgs/lib/libnav2_msgs__rosidl_typesupport_introspection_c.so
/home/nav2-ws/install/nav2_msgs/lib/libnav2_msgs__rosidl_typesupport_c.so
/home/nav2-ws/install/nav2_msgs/lib/libnav2_msgs__rosidl_typesupport_introspection_cpp.so
/home/nav2-ws/install/nav2_msgs/lib/libnav2_msgs__rosidl_typesupport_cpp.so
/home/nav2-ws/install/nav2_msgs/lib/libnav2_msgs__rosidl_generator_py.so
/home/nav2-ws/install/nav2_msgs/share/nav2_msgs/cmake/export_nav2_msgs__rosidl_generator_cExport.cmake
/home/nav2-ws/install/nav2_msgs/share/nav2_msgs/cmake/export_nav2_msgs__rosidl_generator_cExport-release.cmake
/home/nav2-ws/install/nav2_msgs/share/nav2_msgs/cmake/export_nav2_msgs__rosidl_typesupport_fastrtps_cExport.cmake
/home/nav2-ws/install/nav2_msgs/share/nav2_msgs/cmake/export_nav2_msgs__rosidl_typesupport_fastrtps_cExport-release.cmake
/home/nav2-ws/install/nav2_msgs/share/nav2_msgs/cmake/export_nav2_msgs__rosidl_generator_cppExport.cmake
/home/nav2-ws/install/nav2_msgs/share/nav2_msgs/cmake/export_nav2_msgs__rosidl_typesupport_fastrtps_cppExport.cmake
/home/nav2-ws/install/nav2_msgs/share/nav2_msgs/cmake/export_nav2_msgs__rosidl_typesupport_fastrtps_cppExport-release.cmake
/home/nav2-ws/install/nav2_msgs/share/nav2_msgs/cmake/nav2_msgs__rosidl_typesupport_introspection_cExport.cmake
/home/nav2-ws/install/nav2_msgs/share/nav2_msgs/cmake/nav2_msgs__rosidl_typesupport_introspection_cExport-release.cmake
/home/nav2-ws/install/nav2_msgs/share/nav2_msgs/cmake/nav2_msgs__rosidl_typesupport_cExport.cmake
/home/nav2-ws/install/nav2_msgs/share/nav2_msgs/cmake/nav2_msgs__rosidl_typesupport_cExport-release.cmake
/home/nav2-ws/install/nav2_msgs/share/nav2_msgs/cmake/nav2_msgs__rosidl_typesupport_introspection_cppExport.cmake
/home/nav2-ws/install/nav2_msgs/share/nav2_msgs/cmake/nav2_msgs__rosidl_typesupport_introspection_cppExport-release.cmake
/home/nav2-ws/install/nav2_msgs/share/nav2_msgs/cmake/nav2_msgs__rosidl_typesupport_cppExport.cmake
/home/nav2-ws/install/nav2_msgs/share/nav2_msgs/cmake/nav2_msgs__rosidl_typesupport_cppExport-release.cmake
/home/nav2-ws/install/nav2_msgs/share/nav2_msgs/cmake/export_nav2_msgs__rosidl_generator_pyExport.cmake
/home/nav2-ws/install/nav2_msgs/share/nav2_msgs/cmake/export_nav2_msgs__rosidl_generator_pyExport-release.cmake

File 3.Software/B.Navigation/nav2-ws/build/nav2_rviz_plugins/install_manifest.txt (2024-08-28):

/home/nav2-ws/install/nav2_rviz_plugins/lib/libnav2_rviz_plugins.so
/home/nav2-ws/install/nav2_rviz_plugins/share/nav2_rviz_plugins/cmake/nav2_rviz_pluginsExport.cmake
/home/nav2-ws/install/nav2_rviz_plugins/share/nav2_rviz_plugins/cmake/nav2_rviz_pluginsExport-noconfig.cmake

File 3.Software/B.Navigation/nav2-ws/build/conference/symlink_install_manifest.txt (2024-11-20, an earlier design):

/home/nav2-ws/install/conference/lib/conference/libnav.a
/home/nav2-ws/install/conference/lib/conference/demo_nav_retrieval
/home/nav2-ws/install/conference/lib/conference/demo_retrieval_supply
/home/nav2-ws/install/conference/share/ament_index/resource_index/package_run_dependencies/conference
/home/nav2-ws/install/conference/share/ament_index/resource_index/parent_prefix_path/conference
/home/nav2-ws/install/conference/share/conference/environment/ament_prefix_path.sh
/home/nav2-ws/install/conference/share/conference/environment/ament_prefix_path.dsv
/home/nav2-ws/install/conference/share/conference/environment/path.sh
/home/nav2-ws/install/conference/share/conference/environment/path.dsv
/home/nav2-ws/install/conference/share/conference/local_setup.bash
/home/nav2-ws/install/conference/share/conference/local_setup.sh
/home/nav2-ws/install/conference/share/conference/local_setup.zsh
/home/nav2-ws/install/conference/share/conference/local_setup.dsv
/home/nav2-ws/install/conference/share/conference/package.dsv
/home/nav2-ws/install/conference/share/ament_index/resource_index/packages/conference
/home/nav2-ws/install/conference/share/conference/cmake/conferenceConfig.cmake
/home/nav2-ws/install/conference/share/conference/cmake/conferenceConfig-version.cmake
/home/nav2-ws/install/conference/share/conference/package.xml

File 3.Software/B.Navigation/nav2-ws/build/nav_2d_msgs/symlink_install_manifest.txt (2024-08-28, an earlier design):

/home/nav2-ws/install/nav_2d_msgs/share/ament_index/resource_index/rosidl_interfaces/nav_2d_msgs
/home/nav2-ws/install/nav_2d_msgs/include/nav_2d_msgs/nav_2d_msgs/msg/detail/path2_d__functions.h
/home/nav2-ws/install/nav_2d_msgs/include/nav_2d_msgs/nav_2d_msgs/msg/detail/path2_d__struct.h
/home/nav2-ws/install/nav_2d_msgs/include/nav_2d_msgs/nav_2d_msgs/msg/detail/path2_d__type_support.h
/home/nav2-ws/install/nav_2d_msgs/include/nav_2d_msgs/nav_2d_msgs/msg/detail/pose2_d32__functions.h
/home/nav2-ws/install/nav_2d_msgs/include/nav_2d_msgs/nav_2d_msgs/msg/detail/pose2_d32__struct.h
/home/nav2-ws/install/nav_2d_msgs/include/nav_2d_msgs/nav_2d_msgs/msg/detail/pose2_d32__type_support.h
/home/nav2-ws/install/nav_2d_msgs/include/nav_2d_msgs/nav_2d_msgs/msg/detail/pose2_d_stamped__functions.h
/home/nav2-ws/install/nav_2d_msgs/include/nav_2d_msgs/nav_2d_msgs/msg/detail/pose2_d_stamped__struct.h
/home/nav2-ws/install/nav_2d_msgs/include/nav_2d_msgs/nav_2d_msgs/msg/detail/pose2_d_stamped__type_support.h
/home/nav2-ws/install/nav_2d_msgs/include/nav_2d_msgs/nav_2d_msgs/msg/detail/twist2_d32__functions.h
/home/nav2-ws/install/nav_2d_msgs/include/nav_2d_msgs/nav_2d_msgs/msg/detail/twist2_d32__struct.h
/home/nav2-ws/install/nav_2d_msgs/include/nav_2d_msgs/nav_2d_msgs/msg/detail/twist2_d32__type_support.h
/home/nav2-ws/install/nav_2d_msgs/include/nav_2d_msgs/nav_2d_msgs/msg/detail/twist2_d__functions.h
/home/nav2-ws/install/nav_2d_msgs/include/nav_2d_msgs/nav_2d_msgs/msg/detail/twist2_d__struct.h
/home/nav2-ws/install/nav_2d_msgs/include/nav_2d_msgs/nav_2d_msgs/msg/detail/twist2_d__type_support.h
/home/nav2-ws/install/nav_2d_msgs/include/nav_2d_msgs/nav_2d_msgs/msg/detail/twist2_d_stamped__functions.h
/home/nav2-ws/install/nav_2d_msgs/include/nav_2d_msgs/nav_2d_msgs/msg/detail/twist2_d_stamped__struct.h
/home/nav2-ws/install/nav_2d_msgs/include/nav_2d_msgs/nav_2d_msgs/msg/detail/twist2_d_stamped__type_support.h
/home/nav2-ws/install/nav_2d_msgs/include/nav_2d_msgs/nav_2d_msgs/msg/path2_d.h
/home/nav2-ws/install/nav_2d_msgs/include/nav_2d_msgs/nav_2d_msgs/msg/pose2_d32.h
/home/nav2-ws/install/nav_2d_msgs/include/nav_2d_msgs/nav_2d_msgs/msg/pose2_d_stamped.h
/home/nav2-ws/install/nav_2d_msgs/include/nav_2d_msgs/nav_2d_msgs/msg/rosidl_generator_c__visibility_control.h
/home/nav2-ws/install/nav_2d_msgs/include/nav_2d_msgs/nav_2d_msgs/msg/twist2_d.h
/home/nav2-ws/install/nav_2d_msgs/include/nav_2d_msgs/nav_2d_msgs/msg/twist2_d32.h
/home/nav2-ws/install/nav_2d_msgs/include/nav_2d_msgs/nav_2d_msgs/msg/twist2_d_stamped.h
/home/nav2-ws/install/nav_2d_msgs/share/nav_2d_msgs/environment/library_path.sh
/home/nav2-ws/install/nav_2d_msgs/share/nav_2d_msgs/environment/library_path.dsv
/home/nav2-ws/install/nav_2d_msgs/include/nav_2d_msgs/nav_2d_msgs/msg/detail/path2_d__rosidl_typesupport_fastrtps_c.h
/home/nav2-ws/install/nav_2d_msgs/include/nav_2d_msgs/nav_2d_msgs/msg/detail/pose2_d32__rosidl_typesupport_fastrtps_c.h
/home/nav2-ws/install/nav_2d_msgs/include/nav_2d_msgs/nav_2d_msgs/msg/detail/pose2_d_stamped__rosidl_typesupport_fastrtps_c.h
/home/nav2-ws/install/nav_2d_msgs/include/nav_2d_msgs/nav_2d_msgs/msg/detail/twist2_d32__rosidl_typesupport_fastrtps_c.h
/home/nav2-ws/install/nav_2d_msgs/include/nav_2d_msgs/nav_2d_msgs/msg/detail/twist2_d__rosidl_typesupport_fastrtps_c.h
/home/nav2-ws/install/nav_2d_msgs/include/nav_2d_msgs/nav_2d_msgs/msg/detail/twist2_d_stamped__rosidl_typesupport_fastrtps_c.h
/home/nav2-ws/install/nav_2d_msgs/include/nav_2d_msgs/nav_2d_msgs/msg/rosidl_typesupport_fastrtps_c__visibility_control.h
/home/nav2-ws/install/nav_2d_msgs/include/nav_2d_msgs/nav_2d_msgs/msg/detail/path2_d__builder.hpp
/home/nav2-ws/install/nav_2d_msgs/include/nav_2d_msgs/nav_2d_msgs/msg/detail/path2_d__struct.hpp
/home/nav2-ws/install/nav_2d_msgs/include/nav_2d_msgs/nav_2d_msgs/msg/detail/path2_d__traits.hpp
/home/nav2-ws/install/nav_2d_msgs/include/nav_2d_msgs/nav_2d_msgs/msg/detail/pose2_d32__builder.hpp
/home/nav2-ws/install/nav_2d_msgs/include/nav_2d_msgs/nav_2d_msgs/msg/detail/pose2_d32__struct.hpp
/home/nav2-ws/install/nav_2d_msgs/include/nav_2d_msgs/nav_2d_msgs/msg/detail/pose2_d32__traits.hpp
/home/nav2-ws/install/nav_2d_msgs/include/nav_2d_msgs/nav_2d_msgs/msg/detail/pose2_d_stamped__builder.hpp
/home/nav2-ws/install/nav_2d_msgs/include/nav_2d_msgs/nav_2d_msgs/msg/detail/pose2_d_stamped__struct.hpp
/home/nav2-ws/install/nav_2d_msgs/include/nav_2d_msgs/nav_2d_msgs/msg/detail/pose2_d_stamped__traits.hpp
/home/nav2-ws/install/nav_2d_msgs/include/nav_2d_msgs/nav_2d_msgs/msg/detail/twist2_d32__builder.hpp
/home/nav2-ws/install/nav_2d_msgs/include/nav_2d_msgs/nav_2d_msgs/msg/detail/twist2_d32__struct.hpp
/home/nav2-ws/install/nav_2d_msgs/include/nav_2d_msgs/nav_2d_msgs/msg/detail/twist2_d32__traits.hpp
/home/nav2-ws/install/nav_2d_msgs/include/nav_2d_msgs/nav_2d_msgs/msg/detail/twist2_d__builder.hpp
/home/nav2-ws/install/nav_2d_msgs/include/nav_2d_msgs/nav_2d_msgs/msg/detail/twist2_d__struct.hpp
/home/nav2-ws/install/nav_2d_msgs/include/nav_2d_msgs/nav_2d_msgs/msg/detail/twist2_d__traits.hpp
/home/nav2-ws/install/nav_2d_msgs/include/nav_2d_msgs/nav_2d_msgs/msg/detail/twist2_d_stamped__builder.hpp
/home/nav2-ws/install/nav_2d_msgs/include/nav_2d_msgs/nav_2d_msgs/msg/detail/twist2_d_stamped__struct.hpp
/home/nav2-ws/install/nav_2d_msgs/include/nav_2d_msgs/nav_2d_msgs/msg/detail/twist2_d_stamped__traits.hpp
/home/nav2-ws/install/nav_2d_msgs/include/nav_2d_msgs/nav_2d_msgs/msg/path2_d.hpp
/home/nav2-ws/install/nav_2d_msgs/include/nav_2d_msgs/nav_2d_msgs/msg/pose2_d32.hpp
/home/nav2-ws/install/nav_2d_msgs/include/nav_2d_msgs/nav_2d_msgs/msg/pose2_d_stamped.hpp
/home/nav2-ws/install/nav_2d_msgs/include/nav_2d_msgs/nav_2d_msgs/msg/twist2_d.hpp
/home/nav2-ws/install/nav_2d_msgs/include/nav_2d_msgs/nav_2d_msgs/msg/twist2_d32.hpp
/home/nav2-ws/install/nav_2d_msgs/include/nav_2d_msgs/nav_2d_msgs/msg/twist2_d_stamped.hpp
/home/nav2-ws/install/nav_2d_msgs/include/nav_2d_msgs/nav_2d_msgs/msg/detail/path2_d__rosidl_typesupport_fastrtps_cpp.hpp
/home/nav2-ws/install/nav_2d_msgs/include/nav_2d_msgs/nav_2d_msgs/msg/detail/pose2_d32__rosidl_typesupport_fastrtps_cpp.hpp
/home/nav2-ws/install/nav_2d_msgs/include/nav_2d_msgs/nav_2d_msgs/msg/detail/pose2_d_stamped__rosidl_typesupport_fastrtps_cpp.hpp
/home/nav2-ws/install/nav_2d_msgs/include/nav_2d_msgs/nav_2d_msgs/msg/detail/twist2_d32__rosidl_typesupport_fastrtps_cpp.hpp
/home/nav2-ws/install/nav_2d_msgs/include/nav_2d_msgs/nav_2d_msgs/msg/detail/twist2_d__rosidl_typesupport_fastrtps_cpp.hpp
/home/nav2-ws/install/nav_2d_msgs/include/nav_2d_msgs/nav_2d_msgs/msg/detail/twist2_d_stamped__rosidl_typesupport_fastrtps_cpp.hpp
/home/nav2-ws/install/nav_2d_msgs/include/nav_2d_msgs/nav_2d_msgs/msg/rosidl_typesupport_fastrtps_cpp__visibility_control.h
/home/nav2-ws/install/nav_2d_msgs/include/nav_2d_msgs/nav_2d_msgs/msg/detail/path2_d__rosidl_typesupport_introspection_c.h
/home/nav2-ws/install/nav_2d_msgs/include/nav_2d_msgs/nav_2d_msgs/msg/detail/pose2_d32__rosidl_typesupport_introspection_c.h
/home/nav2-ws/install/nav_2d_msgs/include/nav_2d_msgs/nav_2d_msgs/msg/detail/pose2_d_stamped__rosidl_typesupport_introspection_c.h
/home/nav2-ws/install/nav_2d_msgs/include/nav_2d_msgs/nav_2d_msgs/msg/detail/twist2_d32__rosidl_typesupport_introspection_c.h
/home/nav2-ws/install/nav_2d_msgs/include/nav_2d_msgs/nav_2d_msgs/msg/detail/twist2_d__rosidl_typesupport_introspection_c.h
/home/nav2-ws/install/nav_2d_msgs/include/nav_2d_msgs/nav_2d_msgs/msg/detail/twist2_d_stamped__rosidl_typesupport_introspection_c.h
/home/nav2-ws/install/nav_2d_msgs/include/nav_2d_msgs/nav_2d_msgs/msg/rosidl_typesupport_introspection_c__visibility_control.h
/home/nav2-ws/install/nav_2d_msgs/include/nav_2d_msgs/nav_2d_msgs/msg/detail/path2_d__rosidl_typesupport_introspection_cpp.hpp
/home/nav2-ws/install/nav_2d_msgs/include/nav_2d_msgs/nav_2d_msgs/msg/detail/pose2_d32__rosidl_typesupport_introspection_cpp.hpp
/home/nav2-ws/install/nav_2d_msgs/include/nav_2d_msgs/nav_2d_msgs/msg/detail/pose2_d_stamped__rosidl_typesupport_introspection_cpp.hpp
/home/nav2-ws/install/nav_2d_msgs/include/nav_2d_msgs/nav_2d_msgs/msg/detail/twist2_d32__rosidl_typesupport_introspection_cpp.hpp
/home/nav2-ws/install/nav_2d_msgs/include/nav_2d_msgs/nav_2d_msgs/msg/detail/twist2_d__rosidl_typesupport_introspection_cpp.hpp
/home/nav2-ws/install/nav_2d_msgs/include/nav_2d_msgs/nav_2d_msgs/msg/detail/twist2_d_stamped__rosidl_typesupport_introspection_cpp.hpp
/home/nav2-ws/install/nav_2d_msgs/share/nav_2d_msgs/environment/pythonpath.sh
/home/nav2-ws/install/nav_2d_msgs/share/nav_2d_msgs/environment/pythonpath.dsv
/home/nav2-ws/install/nav_2d_msgs/local/lib/python3.10/dist-packages/nav_2d_msgs-1.1.16-py3.10.egg-info/PKG-INFO
/home/nav2-ws/install/nav_2d_msgs/local/lib/python3.10/dist-packages/nav_2d_msgs-1.1.16-py3.10.egg-info/SOURCES.txt
/home/nav2-ws/install/nav_2d_msgs/local/lib/python3.10/dist-packages/nav_2d_msgs-1.1.16-py3.10.egg-info/dependency_links.txt
/home/nav2-ws/install/nav_2d_msgs/local/lib/python3.10/dist-packages/nav_2d_msgs-1.1.16-py3.10.egg-info/top_level.txt
/home/nav2-ws/install/nav_2d_msgs/local/lib/python3.10/dist-packages/nav_2d_msgs/__init__.py
/home/nav2-ws/install/nav_2d_msgs/local/lib/python3.10/dist-packages/nav_2d_msgs/_nav_2d_msgs_s.ep.rosidl_typesupport_c.c
/home/nav2-ws/install/nav_2d_msgs/local/lib/python3.10/dist-packages/nav_2d_msgs/_nav_2d_msgs_s.ep.rosidl_typesupport_fastrtps_c.c
/home/nav2-ws/install/nav_2d_msgs/local/lib/python3.10/dist-packages/nav_2d_msgs/_nav_2d_msgs_s.ep.rosidl_typesupport_introspection_c.c
/home/nav2-ws/install/nav_2d_msgs/local/lib/python3.10/dist-packages/nav_2d_msgs/libnav_2d_msgs__rosidl_generator_py.so
/home/nav2-ws/install/nav_2d_msgs/local/lib/python3.10/dist-packages/nav_2d_msgs/msg/__init__.py
/home/nav2-ws/install/nav_2d_msgs/local/lib/python3.10/dist-packages/nav_2d_msgs/msg/_path2_d.py
/home/nav2-ws/install/nav_2d_msgs/local/lib/python3.10/dist-packages/nav_2d_msgs/msg/_path2_d_s.c
/home/nav2-ws/install/nav_2d_msgs/local/lib/python3.10/dist-packages/nav_2d_msgs/msg/_pose2_d32.py
/home/nav2-ws/install/nav_2d_msgs/local/lib/python3.10/dist-packages/nav_2d_msgs/msg/_pose2_d32_s.c
/home/nav2-ws/install/nav_2d_msgs/local/lib/python3.10/dist-packages/nav_2d_msgs/msg/_pose2_d_stamped.py
/home/nav2-ws/install/nav_2d_msgs/local/lib/python3.10/dist-packages/nav_2d_msgs/msg/_pose2_d_stamped_s.c
/home/nav2-ws/install/nav_2d_msgs/local/lib/python3.10/dist-packages/nav_2d_msgs/msg/_twist2_d.py
/home/nav2-ws/install/nav_2d_msgs/local/lib/python3.10/dist-packages/nav_2d_msgs/msg/_twist2_d32.py
/home/nav2-ws/install/nav_2d_msgs/local/lib/python3.10/dist-packages/nav_2d_msgs/msg/_twist2_d32_s.c
/home/nav2-ws/install/nav_2d_msgs/local/lib/python3.10/dist-packages/nav_2d_msgs/msg/_twist2_d_s.c
/home/nav2-ws/install/nav_2d_msgs/local/lib/python3.10/dist-packages/nav_2d_msgs/msg/_twist2_d_stamped.py
/home/nav2-ws/install/nav_2d_msgs/local/lib/python3.10/dist-packages/nav_2d_msgs/msg/_twist2_d_stamped_s.c
/home/nav2-ws/install/nav_2d_msgs/local/lib/python3.10/dist-packages/nav_2d_msgs/nav_2d_msgs_s__rosidl_typesupport_c.cpython-310-x86_64-linux-gnu.so
/home/nav2-ws/install/nav_2d_msgs/local/lib/python3.10/dist-packages/nav_2d_msgs/nav_2d_msgs_s__rosidl_typesupport_fastrtps_c.cpython-310-x86_64-linux-gnu.so
/home/nav2-ws/install/nav_2d_msgs/local/lib/python3.10/dist-packages/nav_2d_msgs/nav_2d_msgs_s__rosidl_typesupport_introspection_c.cpython-310-x86_64-linux-gnu.so
/home/nav2-ws/install/nav_2d_msgs/local/lib/python3.10/dist-packages/nav_2d_msgs/nav_2d_msgs_s__rosidl_typesupport_fastrtps_c.cpython-310-x86_64-linux-gnu.so
/home/nav2-ws/install/nav_2d_msgs/local/lib/python3.10/dist-packages/nav_2d_msgs/nav_2d_msgs_s__rosidl_typesupport_introspection_c.cpython-310-x86_64-linux-gnu.so
/home/nav2-ws/install/nav_2d_msgs/local/lib/python3.10/dist-packages/nav_2d_msgs/nav_2d_msgs_s__rosidl_typesupport_c.cpython-310-x86_64-linux-gnu.so
/home/nav2-ws/install/nav_2d_msgs/share/nav_2d_msgs/msg/Path2D.idl
/home/nav2-ws/install/nav_2d_msgs/share/nav_2d_msgs/msg/Pose2D32.idl
/home/nav2-ws/install/nav_2d_msgs/share/nav_2d_msgs/msg/Pose2DStamped.idl
/home/nav2-ws/install/nav_2d_msgs/share/nav_2d_msgs/msg/Twist2D.idl
/home/nav2-ws/install/nav_2d_msgs/share/nav_2d_msgs/msg/Twist2D32.idl
/home/nav2-ws/install/nav_2d_msgs/share/nav_2d_msgs/msg/Twist2DStamped.idl
/home/nav2-ws/install/nav_2d_msgs/share/nav_2d_msgs/msg/Path2D.msg
/home/nav2-ws/install/nav_2d_msgs/share/nav_2d_msgs/msg/Pose2D32.msg
/home/nav2-ws/install/nav_2d_msgs/share/nav_2d_msgs/msg/Pose2DStamped.msg
/home/nav2-ws/install/nav_2d_msgs/share/nav_2d_msgs/msg/Twist2D.msg
/home/nav2-ws/install/nav_2d_msgs/share/nav_2d_msgs/msg/Twist2D32.msg
/home/nav2-ws/install/nav_2d_msgs/share/nav_2d_msgs/msg/Twist2DStamped.msg
/home/nav2-ws/install/nav_2d_msgs/share/ament_index/resource_index/package_run_dependencies/nav_2d_msgs
/home/nav2-ws/install/nav_2d_msgs/share/ament_index/resource_index/parent_prefix_path/nav_2d_msgs
/home/nav2-ws/install/nav_2d_msgs/share/nav_2d_msgs/environment/ament_prefix_path.sh
/home/nav2-ws/install/nav_2d_msgs/share/nav_2d_msgs/environment/ament_prefix_path.dsv
/home/nav2-ws/install/nav_2d_msgs/share/nav_2d_msgs/environment/path.sh
/home/nav2-ws/install/nav_2d_msgs/share/nav_2d_msgs/environment/path.dsv
/home/nav2-ws/install/nav_2d_msgs/share/nav_2d_msgs/local_setup.bash
/home/nav2-ws/install/nav_2d_msgs/share/nav_2d_msgs/local_setup.sh
/home/nav2-ws/install/nav_2d_msgs/share/nav_2d_msgs/local_setup.zsh
/home/nav2-ws/install/nav_2d_msgs/share/nav_2d_msgs/local_setup.dsv
/home/nav2-ws/install/nav_2d_msgs/share/nav_2d_msgs/package.dsv
/home/nav2-ws/install/nav_2d_msgs/share/ament_index/resource_index/packages/nav_2d_msgs
/home/nav2-ws/install/nav_2d_msgs/share/nav_2d_msgs/cmake/rosidl_cmake-extras.cmake
/home/nav2-ws/install/nav_2d_msgs/share/nav_2d_msgs/cmake/ament_cmake_export_dependencies-extras.cmake
/home/nav2-ws/install/nav_2d_msgs/share/nav_2d_msgs/cmake/ament_cmake_export_include_directories-extras.cmake
/home/nav2-ws/install/nav_2d_msgs/share/nav_2d_msgs/cmake/ament_cmake_export_libraries-extras.cmake
/home/nav2-ws/install/nav_2d_msgs/share/nav_2d_msgs/cmake/ament_cmake_export_targets-extras.cmake
/home/nav2-ws/install/nav_2d_msgs/share/nav_2d_msgs/cmake/rosidl_cmake_export_typesupport_targets-extras.cmake
/home/nav2-ws/install/nav_2d_msgs/share/nav_2d_msgs/cmake/rosidl_cmake_export_typesupport_libraries-extras.cmake
/home/nav2-ws/install/nav_2d_msgs/share/nav_2d_msgs/cmake/nav_2d_msgsConfig.cmake
/home/nav2-ws/install/nav_2d_msgs/share/nav_2d_msgs/cmake/nav_2d_msgsConfig-version.cmake
/home/nav2-ws/install/nav_2d_msgs/share/nav_2d_msgs/package.xml

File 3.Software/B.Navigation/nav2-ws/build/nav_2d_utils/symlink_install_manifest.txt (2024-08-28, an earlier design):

/home/nav2-ws/install/nav_2d_utils/lib/libconversions.so
/home/nav2-ws/install/nav_2d_utils/lib/libpath_ops.so
/home/nav2-ws/install/nav_2d_utils/lib/libtf_help.so
/home/nav2-ws/install/nav_2d_utils/include//nav_2d_utils/conversions.hpp
/home/nav2-ws/install/nav_2d_utils/include//nav_2d_utils/odom_subscriber.hpp
/home/nav2-ws/install/nav_2d_utils/include//nav_2d_utils/parameters.hpp
/home/nav2-ws/install/nav_2d_utils/include//nav_2d_utils/path_ops.hpp
/home/nav2-ws/install/nav_2d_utils/include//nav_2d_utils/tf_help.hpp
/home/nav2-ws/install/nav_2d_utils/share/nav_2d_utils/environment/library_path.sh
/home/nav2-ws/install/nav_2d_utils/share/nav_2d_utils/environment/library_path.dsv
/home/nav2-ws/install/nav_2d_utils/share/ament_index/resource_index/package_run_dependencies/nav_2d_utils
/home/nav2-ws/install/nav_2d_utils/share/ament_index/resource_index/parent_prefix_path/nav_2d_utils
/home/nav2-ws/install/nav_2d_utils/share/nav_2d_utils/environment/ament_prefix_path.sh
/home/nav2-ws/install/nav_2d_utils/share/nav_2d_utils/environment/ament_prefix_path.dsv
/home/nav2-ws/install/nav_2d_utils/share/nav_2d_utils/environment/path.sh
/home/nav2-ws/install/nav_2d_utils/share/nav_2d_utils/environment/path.dsv
/home/nav2-ws/install/nav_2d_utils/share/nav_2d_utils/local_setup.bash
/home/nav2-ws/install/nav_2d_utils/share/nav_2d_utils/local_setup.sh
/home/nav2-ws/install/nav_2d_utils/share/nav_2d_utils/local_setup.zsh
/home/nav2-ws/install/nav_2d_utils/share/nav_2d_utils/local_setup.dsv
/home/nav2-ws/install/nav_2d_utils/share/nav_2d_utils/package.dsv
/home/nav2-ws/install/nav_2d_utils/share/ament_index/resource_index/packages/nav_2d_utils
/home/nav2-ws/install/nav_2d_utils/share/nav_2d_utils/cmake/ament_cmake_export_include_directories-extras.cmake
/home/nav2-ws/install/nav_2d_utils/share/nav_2d_utils/cmake/ament_cmake_export_libraries-extras.cmake
/home/nav2-ws/install/nav_2d_utils/share/nav_2d_utils/cmake/ament_cmake_export_dependencies-extras.cmake
/home/nav2-ws/install/nav_2d_utils/share/nav_2d_utils/cmake/nav_2d_utilsConfig.cmake
/home/nav2-ws/install/nav_2d_utils/share/nav_2d_utils/cmake/nav_2d_utilsConfig-version.cmake
/home/nav2-ws/install/nav_2d_utils/share/nav_2d_utils/package.xml

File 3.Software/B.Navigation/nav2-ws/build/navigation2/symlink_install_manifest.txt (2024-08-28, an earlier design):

/home/nav2-ws/install/navigation2/share/ament_index/resource_index/package_run_dependencies/navigation2
/home/nav2-ws/install/navigation2/share/ament_index/resource_index/parent_prefix_path/navigation2
/home/nav2-ws/install/navigation2/share/navigation2/environment/ament_prefix_path.sh
/home/nav2-ws/install/navigation2/share/navigation2/environment/ament_prefix_path.dsv
/home/nav2-ws/install/navigation2/share/navigation2/environment/path.sh
/home/nav2-ws/install/navigation2/share/navigation2/environment/path.dsv
/home/nav2-ws/install/navigation2/share/navigation2/local_setup.bash
/home/nav2-ws/install/navigation2/share/navigation2/local_setup.sh
/home/nav2-ws/install/navigation2/share/navigation2/local_setup.zsh
/home/nav2-ws/install/navigation2/share/navigation2/local_setup.dsv
/home/nav2-ws/install/navigation2/share/navigation2/package.dsv
/home/nav2-ws/install/navigation2/share/ament_index/resource_index/packages/navigation2
/home/nav2-ws/install/navigation2/share/navigation2/cmake/navigation2Config.cmake
/home/nav2-ws/install/navigation2/share/navigation2/cmake/navigation2Config-version.cmake
/home/nav2-ws/install/navigation2/share/navigation2/package.xml

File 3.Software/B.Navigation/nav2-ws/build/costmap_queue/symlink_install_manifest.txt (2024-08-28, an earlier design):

/home/nav2-ws/install/costmap_queue/lib/libcostmap_queue.so
/home/nav2-ws/install/costmap_queue/include//costmap_queue/costmap_queue.hpp
/home/nav2-ws/install/costmap_queue/include//costmap_queue/limited_costmap_queue.hpp
/home/nav2-ws/install/costmap_queue/include//costmap_queue/map_based_queue.hpp
/home/nav2-ws/install/costmap_queue/share/costmap_queue/environment/library_path.sh
/home/nav2-ws/install/costmap_queue/share/costmap_queue/environment/library_path.dsv
/home/nav2-ws/install/costmap_queue/share/ament_index/resource_index/package_run_dependencies/costmap_queue
/home/nav2-ws/install/costmap_queue/share/ament_index/resource_index/parent_prefix_path/costmap_queue
/home/nav2-ws/install/costmap_queue/share/costmap_queue/environment/ament_prefix_path.sh
/home/nav2-ws/install/costmap_queue/share/costmap_queue/environment/ament_prefix_path.dsv
/home/nav2-ws/install/costmap_queue/share/costmap_queue/environment/path.sh
/home/nav2-ws/install/costmap_queue/share/costmap_queue/environment/path.dsv
/home/nav2-ws/install/costmap_queue/share/costmap_queue/local_setup.bash
/home/nav2-ws/install/costmap_queue/share/costmap_queue/local_setup.sh
/home/nav2-ws/install/costmap_queue/share/costmap_queue/local_setup.zsh
/home/nav2-ws/install/costmap_queue/share/costmap_queue/local_setup.dsv
/home/nav2-ws/install/costmap_queue/share/costmap_queue/package.dsv
/home/nav2-ws/install/costmap_queue/share/ament_index/resource_index/packages/costmap_queue
/home/nav2-ws/install/costmap_queue/share/costmap_queue/cmake/ament_cmake_export_include_directories-extras.cmake
/home/nav2-ws/install/costmap_queue/share/costmap_queue/cmake/ament_cmake_export_libraries-extras.cmake
/home/nav2-ws/install/costmap_queue/share/costmap_queue/cmake/costmap_queueConfig.cmake
/home/nav2-ws/install/costmap_queue/share/costmap_queue/cmake/costmap_queueConfig-version.cmake
/home/nav2-ws/install/costmap_queue/share/costmap_queue/package.xml

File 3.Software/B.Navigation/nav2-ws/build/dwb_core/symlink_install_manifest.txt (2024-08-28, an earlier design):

/home/nav2-ws/install/dwb_core/lib/libdwb_core.so
/home/nav2-ws/install/dwb_core/include//dwb_core/dwb_local_planner.hpp
/home/nav2-ws/install/dwb_core/include//dwb_core/exceptions.hpp
/home/nav2-ws/install/dwb_core/include//dwb_core/illegal_trajectory_tracker.hpp
/home/nav2-ws/install/dwb_core/include//dwb_core/publisher.hpp
/home/nav2-ws/install/dwb_core/include//dwb_core/trajectory_critic.hpp
/home/nav2-ws/install/dwb_core/include//dwb_core/trajectory_generator.hpp
/home/nav2-ws/install/dwb_core/include//dwb_core/trajectory_utils.hpp
/home/nav2-ws/install/dwb_core/share/dwb_core/environment/library_path.sh
/home/nav2-ws/install/dwb_core/share/dwb_core/environment/library_path.dsv
/home/nav2-ws/install/dwb_core/share/dwb_core//local_planner_plugin.xml
/home/nav2-ws/install/dwb_core/share/ament_index/resource_index/package_run_dependencies/dwb_core
/home/nav2-ws/install/dwb_core/share/ament_index/resource_index/parent_prefix_path/dwb_core
/home/nav2-ws/install/dwb_core/share/dwb_core/environment/ament_prefix_path.sh
/home/nav2-ws/install/dwb_core/share/dwb_core/environment/ament_prefix_path.dsv
/home/nav2-ws/install/dwb_core/share/dwb_core/environment/path.sh
/home/nav2-ws/install/dwb_core/share/dwb_core/environment/path.dsv
/home/nav2-ws/install/dwb_core/share/dwb_core/local_setup.bash
/home/nav2-ws/install/dwb_core/share/dwb_core/local_setup.sh
/home/nav2-ws/install/dwb_core/share/dwb_core/local_setup.zsh
/home/nav2-ws/install/dwb_core/share/dwb_core/local_setup.dsv
/home/nav2-ws/install/dwb_core/share/dwb_core/package.dsv
/home/nav2-ws/install/dwb_core/share/ament_index/resource_index/packages/dwb_core
/home/nav2-ws/install/dwb_core/share/ament_index/resource_index/nav2_core__pluginlib__plugin/dwb_core
/home/nav2-ws/install/dwb_core/share/dwb_core/cmake/ament_cmake_export_include_directories-extras.cmake
/home/nav2-ws/install/dwb_core/share/dwb_core/cmake/ament_cmake_export_libraries-extras.cmake
/home/nav2-ws/install/dwb_core/share/dwb_core/cmake/ament_cmake_export_dependencies-extras.cmake
/home/nav2-ws/install/dwb_core/share/dwb_core/cmake/dwb_coreConfig.cmake
/home/nav2-ws/install/dwb_core/share/dwb_core/cmake/dwb_coreConfig-version.cmake
/home/nav2-ws/install/dwb_core/share/dwb_core/package.xml

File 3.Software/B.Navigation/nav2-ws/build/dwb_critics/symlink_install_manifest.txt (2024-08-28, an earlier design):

/home/nav2-ws/install/dwb_critics/lib/libdwb_critics.so
/home/nav2-ws/install/dwb_critics/include//dwb_critics/alignment_util.hpp
/home/nav2-ws/install/dwb_critics/include//dwb_critics/base_obstacle.hpp
/home/nav2-ws/install/dwb_critics/include//dwb_critics/goal_align.hpp
/home/nav2-ws/install/dwb_critics/include//dwb_critics/goal_dist.hpp
/home/nav2-ws/install/dwb_critics/include//dwb_critics/line_iterator.hpp
/home/nav2-ws/install/dwb_critics/include//dwb_critics/map_grid.hpp
/home/nav2-ws/install/dwb_critics/include//dwb_critics/obstacle_footprint.hpp
/home/nav2-ws/install/dwb_critics/include//dwb_critics/oscillation.hpp
/home/nav2-ws/install/dwb_critics/include//dwb_critics/path_align.hpp
/home/nav2-ws/install/dwb_critics/include//dwb_critics/path_dist.hpp
/home/nav2-ws/install/dwb_critics/include//dwb_critics/prefer_forward.hpp
/home/nav2-ws/install/dwb_critics/include//dwb_critics/rotate_to_goal.hpp
/home/nav2-ws/install/dwb_critics/include//dwb_critics/twirling.hpp
/home/nav2-ws/install/dwb_critics/share/dwb_critics/default_critics.xml
/home/nav2-ws/install/dwb_critics/share/dwb_critics/environment/library_path.sh
/home/nav2-ws/install/dwb_critics/share/dwb_critics/environment/library_path.dsv
/home/nav2-ws/install/dwb_critics/share/dwb_critics//default_critics.xml
/home/nav2-ws/install/dwb_critics/share/ament_index/resource_index/package_run_dependencies/dwb_critics
/home/nav2-ws/install/dwb_critics/share/ament_index/resource_index/parent_prefix_path/dwb_critics
/home/nav2-ws/install/dwb_critics/share/dwb_critics/environment/ament_prefix_path.sh
/home/nav2-ws/install/dwb_critics/share/dwb_critics/environment/ament_prefix_path.dsv
/home/nav2-ws/install/dwb_critics/share/dwb_critics/environment/path.sh
/home/nav2-ws/install/dwb_critics/share/dwb_critics/environment/path.dsv
/home/nav2-ws/install/dwb_critics/share/dwb_critics/local_setup.bash
/home/nav2-ws/install/dwb_critics/share/dwb_critics/local_setup.sh
/home/nav2-ws/install/dwb_critics/share/dwb_critics/local_setup.zsh
/home/nav2-ws/install/dwb_critics/share/dwb_critics/local_setup.dsv
/home/nav2-ws/install/dwb_critics/share/dwb_critics/package.dsv
/home/nav2-ws/install/dwb_critics/share/ament_index/resource_index/packages/dwb_critics
/home/nav2-ws/install/dwb_critics/share/ament_index/resource_index/dwb_core__pluginlib__plugin/dwb_critics
/home/nav2-ws/install/dwb_critics/share/dwb_critics/cmake/ament_cmake_export_include_directories-extras.cmake
/home/nav2-ws/install/dwb_critics/share/dwb_critics/cmake/ament_cmake_export_libraries-extras.cmake
/home/nav2-ws/install/dwb_critics/share/dwb_critics/cmake/ament_cmake_export_dependencies-extras.cmake
/home/nav2-ws/install/dwb_critics/share/dwb_critics/cmake/dwb_criticsConfig.cmake
/home/nav2-ws/install/dwb_critics/share/dwb_critics/cmake/dwb_criticsConfig-version.cmake
/home/nav2-ws/install/dwb_critics/share/dwb_critics/package.xml

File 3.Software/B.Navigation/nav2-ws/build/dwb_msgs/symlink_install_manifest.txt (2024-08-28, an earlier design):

/home/nav2-ws/install/dwb_msgs/share/ament_index/resource_index/rosidl_interfaces/dwb_msgs
/home/nav2-ws/install/dwb_msgs/include/dwb_msgs/dwb_msgs/msg/critic_score.h
/home/nav2-ws/install/dwb_msgs/include/dwb_msgs/dwb_msgs/msg/detail/critic_score__functions.h
/home/nav2-ws/install/dwb_msgs/include/dwb_msgs/dwb_msgs/msg/detail/critic_score__struct.h
/home/nav2-ws/install/dwb_msgs/include/dwb_msgs/dwb_msgs/msg/detail/critic_score__type_support.h
/home/nav2-ws/install/dwb_msgs/include/dwb_msgs/dwb_msgs/msg/detail/local_plan_evaluation__functions.h
/home/nav2-ws/install/dwb_msgs/include/dwb_msgs/dwb_msgs/msg/detail/local_plan_evaluation__struct.h
/home/nav2-ws/install/dwb_msgs/include/dwb_msgs/dwb_msgs/msg/detail/local_plan_evaluation__type_support.h
/home/nav2-ws/install/dwb_msgs/include/dwb_msgs/dwb_msgs/msg/detail/trajectory2_d__functions.h
/home/nav2-ws/install/dwb_msgs/include/dwb_msgs/dwb_msgs/msg/detail/trajectory2_d__struct.h
/home/nav2-ws/install/dwb_msgs/include/dwb_msgs/dwb_msgs/msg/detail/trajectory2_d__type_support.h
/home/nav2-ws/install/dwb_msgs/include/dwb_msgs/dwb_msgs/msg/detail/trajectory_score__functions.h
/home/nav2-ws/install/dwb_msgs/include/dwb_msgs/dwb_msgs/msg/detail/trajectory_score__struct.h
/home/nav2-ws/install/dwb_msgs/include/dwb_msgs/dwb_msgs/msg/detail/trajectory_score__type_support.h
/home/nav2-ws/install/dwb_msgs/include/dwb_msgs/dwb_msgs/msg/local_plan_evaluation.h
/home/nav2-ws/install/dwb_msgs/include/dwb_msgs/dwb_msgs/msg/rosidl_generator_c__visibility_control.h
/home/nav2-ws/install/dwb_msgs/include/dwb_msgs/dwb_msgs/msg/trajectory2_d.h
/home/nav2-ws/install/dwb_msgs/include/dwb_msgs/dwb_msgs/msg/trajectory_score.h
/home/nav2-ws/install/dwb_msgs/include/dwb_msgs/dwb_msgs/srv/debug_local_plan.h
/home/nav2-ws/install/dwb_msgs/include/dwb_msgs/dwb_msgs/srv/detail/debug_local_plan__functions.h
/home/nav2-ws/install/dwb_msgs/include/dwb_msgs/dwb_msgs/srv/detail/debug_local_plan__struct.h
/home/nav2-ws/install/dwb_msgs/include/dwb_msgs/dwb_msgs/srv/detail/debug_local_plan__type_support.h
/home/nav2-ws/install/dwb_msgs/include/dwb_msgs/dwb_msgs/srv/detail/generate_trajectory__functions.h
/home/nav2-ws/install/dwb_msgs/include/dwb_msgs/dwb_msgs/srv/detail/generate_trajectory__struct.h
/home/nav2-ws/install/dwb_msgs/include/dwb_msgs/dwb_msgs/srv/detail/generate_trajectory__type_support.h
/home/nav2-ws/install/dwb_msgs/include/dwb_msgs/dwb_msgs/srv/detail/generate_twists__functions.h
/home/nav2-ws/install/dwb_msgs/include/dwb_msgs/dwb_msgs/srv/detail/generate_twists__struct.h
/home/nav2-ws/install/dwb_msgs/include/dwb_msgs/dwb_msgs/srv/detail/generate_twists__type_support.h
/home/nav2-ws/install/dwb_msgs/include/dwb_msgs/dwb_msgs/srv/detail/get_critic_score__functions.h
/home/nav2-ws/install/dwb_msgs/include/dwb_msgs/dwb_msgs/srv/detail/get_critic_score__struct.h
/home/nav2-ws/install/dwb_msgs/include/dwb_msgs/dwb_msgs/srv/detail/get_critic_score__type_support.h
/home/nav2-ws/install/dwb_msgs/include/dwb_msgs/dwb_msgs/srv/detail/score_trajectory__functions.h
/home/nav2-ws/install/dwb_msgs/include/dwb_msgs/dwb_msgs/srv/detail/score_trajectory__struct.h
/home/nav2-ws/install/dwb_msgs/include/dwb_msgs/dwb_msgs/srv/detail/score_trajectory__type_support.h
/home/nav2-ws/install/dwb_msgs/include/dwb_msgs/dwb_msgs/srv/generate_trajectory.h
/home/nav2-ws/install/dwb_msgs/include/dwb_msgs/dwb_msgs/srv/generate_twists.h
/home/nav2-ws/install/dwb_msgs/include/dwb_msgs/dwb_msgs/srv/get_critic_score.h
/home/nav2-ws/install/dwb_msgs/include/dwb_msgs/dwb_msgs/srv/score_trajectory.h
/home/nav2-ws/install/dwb_msgs/share/dwb_msgs/environment/library_path.sh
/home/nav2-ws/install/dwb_msgs/share/dwb_msgs/environment/library_path.dsv
/home/nav2-ws/install/dwb_msgs/include/dwb_msgs/dwb_msgs/msg/detail/critic_score__rosidl_typesupport_fastrtps_c.h
/home/nav2-ws/install/dwb_msgs/include/dwb_msgs/dwb_msgs/msg/detail/local_plan_evaluation__rosidl_typesupport_fastrtps_c.h
/home/nav2-ws/install/dwb_msgs/include/dwb_msgs/dwb_msgs/msg/detail/trajectory2_d__rosidl_typesupport_fastrtps_c.h
/home/nav2-ws/install/dwb_msgs/include/dwb_msgs/dwb_msgs/msg/detail/trajectory_score__rosidl_typesupport_fastrtps_c.h
/home/nav2-ws/install/dwb_msgs/include/dwb_msgs/dwb_msgs/msg/rosidl_typesupport_fastrtps_c__visibility_control.h
/home/nav2-ws/install/dwb_msgs/include/dwb_msgs/dwb_msgs/srv/detail/debug_local_plan__rosidl_typesupport_fastrtps_c.h
/home/nav2-ws/install/dwb_msgs/include/dwb_msgs/dwb_msgs/srv/detail/generate_trajectory__rosidl_typesupport_fastrtps_c.h
/home/nav2-ws/install/dwb_msgs/include/dwb_msgs/dwb_msgs/srv/detail/generate_twists__rosidl_typesupport_fastrtps_c.h
/home/nav2-ws/install/dwb_msgs/include/dwb_msgs/dwb_msgs/srv/detail/get_critic_score__rosidl_typesupport_fastrtps_c.h
/home/nav2-ws/install/dwb_msgs/include/dwb_msgs/dwb_msgs/srv/detail/score_trajectory__rosidl_typesupport_fastrtps_c.h
/home/nav2-ws/install/dwb_msgs/include/dwb_msgs/dwb_msgs/msg/critic_score.hpp
/home/nav2-ws/install/dwb_msgs/include/dwb_msgs/dwb_msgs/msg/detail/critic_score__builder.hpp
/home/nav2-ws/install/dwb_msgs/include/dwb_msgs/dwb_msgs/msg/detail/critic_score__struct.hpp
/home/nav2-ws/install/dwb_msgs/include/dwb_msgs/dwb_msgs/msg/detail/critic_score__traits.hpp
/home/nav2-ws/install/dwb_msgs/include/dwb_msgs/dwb_msgs/msg/detail/local_plan_evaluation__builder.hpp
/home/nav2-ws/install/dwb_msgs/include/dwb_msgs/dwb_msgs/msg/detail/local_plan_evaluation__struct.hpp
/home/nav2-ws/install/dwb_msgs/include/dwb_msgs/dwb_msgs/msg/detail/local_plan_evaluation__traits.hpp
/home/nav2-ws/install/dwb_msgs/include/dwb_msgs/dwb_msgs/msg/detail/trajectory2_d__builder.hpp
/home/nav2-ws/install/dwb_msgs/include/dwb_msgs/dwb_msgs/msg/detail/trajectory2_d__struct.hpp
/home/nav2-ws/install/dwb_msgs/include/dwb_msgs/dwb_msgs/msg/detail/trajectory2_d__traits.hpp
/home/nav2-ws/install/dwb_msgs/include/dwb_msgs/dwb_msgs/msg/detail/trajectory_score__builder.hpp
/home/nav2-ws/install/dwb_msgs/include/dwb_msgs/dwb_msgs/msg/detail/trajectory_score__struct.hpp
/home/nav2-ws/install/dwb_msgs/include/dwb_msgs/dwb_msgs/msg/detail/trajectory_score__traits.hpp
/home/nav2-ws/install/dwb_msgs/include/dwb_msgs/dwb_msgs/msg/local_plan_evaluation.hpp
/home/nav2-ws/install/dwb_msgs/include/dwb_msgs/dwb_msgs/msg/trajectory2_d.hpp
/home/nav2-ws/install/dwb_msgs/include/dwb_msgs/dwb_msgs/msg/trajectory_score.hpp
/home/nav2-ws/install/dwb_msgs/include/dwb_msgs/dwb_msgs/srv/debug_local_plan.hpp
/home/nav2-ws/install/dwb_msgs/include/dwb_msgs/dwb_msgs/srv/detail/debug_local_plan__builder.hpp
/home/nav2-ws/install/dwb_msgs/include/dwb_msgs/dwb_msgs/srv/detail/debug_local_plan__struct.hpp
/home/nav2-ws/install/dwb_msgs/include/dwb_msgs/dwb_msgs/srv/detail/debug_local_plan__traits.hpp
/home/nav2-ws/install/dwb_msgs/include/dwb_msgs/dwb_msgs/srv/detail/generate_trajectory__builder.hpp
/home/nav2-ws/install/dwb_msgs/include/dwb_msgs/dwb_msgs/srv/detail/generate_trajectory__struct.hpp
/home/nav2-ws/install/dwb_msgs/include/dwb_msgs/dwb_msgs/srv/detail/generate_trajectory__traits.hpp
/home/nav2-ws/install/dwb_msgs/include/dwb_msgs/dwb_msgs/srv/detail/generate_twists__builder.hpp
/home/nav2-ws/install/dwb_msgs/include/dwb_msgs/dwb_msgs/srv/detail/generate_twists__struct.hpp
/home/nav2-ws/install/dwb_msgs/include/dwb_msgs/dwb_msgs/srv/detail/generate_twists__traits.hpp
/home/nav2-ws/install/dwb_msgs/include/dwb_msgs/dwb_msgs/srv/detail/get_critic_score__builder.hpp
/home/nav2-ws/install/dwb_msgs/include/dwb_msgs/dwb_msgs/srv/detail/get_critic_score__struct.hpp
/home/nav2-ws/install/dwb_msgs/include/dwb_msgs/dwb_msgs/srv/detail/get_critic_score__traits.hpp
/home/nav2-ws/install/dwb_msgs/include/dwb_msgs/dwb_msgs/srv/detail/score_trajectory__builder.hpp
/home/nav2-ws/install/dwb_msgs/include/dwb_msgs/dwb_msgs/srv/detail/score_trajectory__struct.hpp
/home/nav2-ws/install/dwb_msgs/include/dwb_msgs/dwb_msgs/srv/detail/score_trajectory__traits.hpp
/home/nav2-ws/install/dwb_msgs/include/dwb_msgs/dwb_msgs/srv/generate_trajectory.hpp
/home/nav2-ws/install/dwb_msgs/include/dwb_msgs/dwb_msgs/srv/generate_twists.hpp
/home/nav2-ws/install/dwb_msgs/include/dwb_msgs/dwb_msgs/srv/get_critic_score.hpp
/home/nav2-ws/install/dwb_msgs/include/dwb_msgs/dwb_msgs/srv/score_trajectory.hpp
/home/nav2-ws/install/dwb_msgs/include/dwb_msgs/dwb_msgs/msg/detail/critic_score__rosidl_typesupport_fastrtps_cpp.hpp
/home/nav2-ws/install/dwb_msgs/include/dwb_msgs/dwb_msgs/msg/detail/local_plan_evaluation__rosidl_typesupport_fastrtps_cpp.hpp
/home/nav2-ws/install/dwb_msgs/include/dwb_msgs/dwb_msgs/msg/detail/trajectory2_d__rosidl_typesupport_fastrtps_cpp.hpp
/home/nav2-ws/install/dwb_msgs/include/dwb_msgs/dwb_msgs/msg/detail/trajectory_score__rosidl_typesupport_fastrtps_cpp.hpp
/home/nav2-ws/install/dwb_msgs/include/dwb_msgs/dwb_msgs/msg/rosidl_typesupport_fastrtps_cpp__visibility_control.h
/home/nav2-ws/install/dwb_msgs/include/dwb_msgs/dwb_msgs/srv/detail/debug_local_plan__rosidl_typesupport_fastrtps_cpp.hpp
/home/nav2-ws/install/dwb_msgs/include/dwb_msgs/dwb_msgs/srv/detail/generate_trajectory__rosidl_typesupport_fastrtps_cpp.hpp
/home/nav2-ws/install/dwb_msgs/include/dwb_msgs/dwb_msgs/srv/detail/generate_twists__rosidl_typesupport_fastrtps_cpp.hpp
/home/nav2-ws/install/dwb_msgs/include/dwb_msgs/dwb_msgs/srv/detail/get_critic_score__rosidl_typesupport_fastrtps_cpp.hpp
/home/nav2-ws/install/dwb_msgs/include/dwb_msgs/dwb_msgs/srv/detail/score_trajectory__rosidl_typesupport_fastrtps_cpp.hpp
/home/nav2-ws/install/dwb_msgs/include/dwb_msgs/dwb_msgs/msg/detail/critic_score__rosidl_typesupport_introspection_c.h
/home/nav2-ws/install/dwb_msgs/include/dwb_msgs/dwb_msgs/msg/detail/local_plan_evaluation__rosidl_typesupport_introspection_c.h
/home/nav2-ws/install/dwb_msgs/include/dwb_msgs/dwb_msgs/msg/detail/trajectory2_d__rosidl_typesupport_introspection_c.h
/home/nav2-ws/install/dwb_msgs/include/dwb_msgs/dwb_msgs/msg/detail/trajectory_score__rosidl_typesupport_introspection_c.h
/home/nav2-ws/install/dwb_msgs/include/dwb_msgs/dwb_msgs/msg/rosidl_typesupport_introspection_c__visibility_control.h
/home/nav2-ws/install/dwb_msgs/include/dwb_msgs/dwb_msgs/srv/detail/debug_local_plan__rosidl_typesupport_introspection_c.h
/home/nav2-ws/install/dwb_msgs/include/dwb_msgs/dwb_msgs/srv/detail/generate_trajectory__rosidl_typesupport_introspection_c.h
/home/nav2-ws/install/dwb_msgs/include/dwb_msgs/dwb_msgs/srv/detail/generate_twists__rosidl_typesupport_introspection_c.h
/home/nav2-ws/install/dwb_msgs/include/dwb_msgs/dwb_msgs/srv/detail/get_critic_score__rosidl_typesupport_introspection_c.h
/home/nav2-ws/install/dwb_msgs/include/dwb_msgs/dwb_msgs/srv/detail/score_trajectory__rosidl_typesupport_introspection_c.h
/home/nav2-ws/install/dwb_msgs/include/dwb_msgs/dwb_msgs/msg/detail/critic_score__rosidl_typesupport_introspection_cpp.hpp
/home/nav2-ws/install/dwb_msgs/include/dwb_msgs/dwb_msgs/msg/detail/local_plan_evaluation__rosidl_typesupport_introspection_cpp.hpp
/home/nav2-ws/install/dwb_msgs/include/dwb_msgs/dwb_msgs/msg/detail/trajectory2_d__rosidl_typesupport_introspection_cpp.hpp
/home/nav2-ws/install/dwb_msgs/include/dwb_msgs/dwb_msgs/msg/detail/trajectory_score__rosidl_typesupport_introspection_cpp.hpp
/home/nav2-ws/install/dwb_msgs/include/dwb_msgs/dwb_msgs/srv/detail/debug_local_plan__rosidl_typesupport_introspection_cpp.hpp
/home/nav2-ws/install/dwb_msgs/include/dwb_msgs/dwb_msgs/srv/detail/generate_trajectory__rosidl_typesupport_introspection_cpp.hpp
/home/nav2-ws/install/dwb_msgs/include/dwb_msgs/dwb_msgs/srv/detail/generate_twists__rosidl_typesupport_introspection_cpp.hpp
/home/nav2-ws/install/dwb_msgs/include/dwb_msgs/dwb_msgs/srv/detail/get_critic_score__rosidl_typesupport_introspection_cpp.hpp
/home/nav2-ws/install/dwb_msgs/include/dwb_msgs/dwb_msgs/srv/detail/score_trajectory__rosidl_typesupport_introspection_cpp.hpp
/home/nav2-ws/install/dwb_msgs/share/dwb_msgs/environment/pythonpath.sh
/home/nav2-ws/install/dwb_msgs/share/dwb_msgs/environment/pythonpath.dsv
/home/nav2-ws/install/dwb_msgs/local/lib/python3.10/dist-packages/dwb_msgs-1.1.16-py3.10.egg-info/PKG-INFO
/home/nav2-ws/install/dwb_msgs/local/lib/python3.10/dist-packages/dwb_msgs-1.1.16-py3.10.egg-info/SOURCES.txt
/home/nav2-ws/install/dwb_msgs/local/lib/python3.10/dist-packages/dwb_msgs-1.1.16-py3.10.egg-info/dependency_links.txt
/home/nav2-ws/install/dwb_msgs/local/lib/python3.10/dist-packages/dwb_msgs-1.1.16-py3.10.egg-info/top_level.txt
/home/nav2-ws/install/dwb_msgs/local/lib/python3.10/dist-packages/dwb_msgs/__init__.py
/home/nav2-ws/install/dwb_msgs/local/lib/python3.10/dist-packages/dwb_msgs/_dwb_msgs_s.ep.rosidl_typesupport_c.c
/home/nav2-ws/install/dwb_msgs/local/lib/python3.10/dist-packages/dwb_msgs/_dwb_msgs_s.ep.rosidl_typesupport_fastrtps_c.c
/home/nav2-ws/install/dwb_msgs/local/lib/python3.10/dist-packages/dwb_msgs/_dwb_msgs_s.ep.rosidl_typesupport_introspection_c.c
/home/nav2-ws/install/dwb_msgs/local/lib/python3.10/dist-packages/dwb_msgs/dwb_msgs_s__rosidl_typesupport_c.cpython-310-x86_64-linux-gnu.so
/home/nav2-ws/install/dwb_msgs/local/lib/python3.10/dist-packages/dwb_msgs/dwb_msgs_s__rosidl_typesupport_fastrtps_c.cpython-310-x86_64-linux-gnu.so
/home/nav2-ws/install/dwb_msgs/local/lib/python3.10/dist-packages/dwb_msgs/dwb_msgs_s__rosidl_typesupport_introspection_c.cpython-310-x86_64-linux-gnu.so
/home/nav2-ws/install/dwb_msgs/local/lib/python3.10/dist-packages/dwb_msgs/libdwb_msgs__rosidl_generator_py.so
/home/nav2-ws/install/dwb_msgs/local/lib/python3.10/dist-packages/dwb_msgs/msg/__init__.py
/home/nav2-ws/install/dwb_msgs/local/lib/python3.10/dist-packages/dwb_msgs/msg/_critic_score.py
/home/nav2-ws/install/dwb_msgs/local/lib/python3.10/dist-packages/dwb_msgs/msg/_critic_score_s.c
/home/nav2-ws/install/dwb_msgs/local/lib/python3.10/dist-packages/dwb_msgs/msg/_local_plan_evaluation.py
/home/nav2-ws/install/dwb_msgs/local/lib/python3.10/dist-packages/dwb_msgs/msg/_local_plan_evaluation_s.c
/home/nav2-ws/install/dwb_msgs/local/lib/python3.10/dist-packages/dwb_msgs/msg/_trajectory2_d.py
/home/nav2-ws/install/dwb_msgs/local/lib/python3.10/dist-packages/dwb_msgs/msg/_trajectory2_d_s.c
/home/nav2-ws/install/dwb_msgs/local/lib/python3.10/dist-packages/dwb_msgs/msg/_trajectory_score.py
/home/nav2-ws/install/dwb_msgs/local/lib/python3.10/dist-packages/dwb_msgs/msg/_trajectory_score_s.c
/home/nav2-ws/install/dwb_msgs/local/lib/python3.10/dist-packages/dwb_msgs/srv/__init__.py
/home/nav2-ws/install/dwb_msgs/local/lib/python3.10/dist-packages/dwb_msgs/srv/_debug_local_plan.py
/home/nav2-ws/install/dwb_msgs/local/lib/python3.10/dist-packages/dwb_msgs/srv/_debug_local_plan_s.c
/home/nav2-ws/install/dwb_msgs/local/lib/python3.10/dist-packages/dwb_msgs/srv/_generate_trajectory.py
/home/nav2-ws/install/dwb_msgs/local/lib/python3.10/dist-packages/dwb_msgs/srv/_generate_trajectory_s.c
/home/nav2-ws/install/dwb_msgs/local/lib/python3.10/dist-packages/dwb_msgs/srv/_generate_twists.py
/home/nav2-ws/install/dwb_msgs/local/lib/python3.10/dist-packages/dwb_msgs/srv/_generate_twists_s.c
/home/nav2-ws/install/dwb_msgs/local/lib/python3.10/dist-packages/dwb_msgs/srv/_get_critic_score.py
/home/nav2-ws/install/dwb_msgs/local/lib/python3.10/dist-packages/dwb_msgs/srv/_get_critic_score_s.c
/home/nav2-ws/install/dwb_msgs/local/lib/python3.10/dist-packages/dwb_msgs/srv/_score_trajectory.py
/home/nav2-ws/install/dwb_msgs/local/lib/python3.10/dist-packages/dwb_msgs/srv/_score_trajectory_s.c
/home/nav2-ws/install/dwb_msgs/local/lib/python3.10/dist-packages/dwb_msgs/dwb_msgs_s__rosidl_typesupport_fastrtps_c.cpython-310-x86_64-linux-gnu.so
/home/nav2-ws/install/dwb_msgs/local/lib/python3.10/dist-packages/dwb_msgs/dwb_msgs_s__rosidl_typesupport_introspection_c.cpython-310-x86_64-linux-gnu.so
/home/nav2-ws/install/dwb_msgs/local/lib/python3.10/dist-packages/dwb_msgs/dwb_msgs_s__rosidl_typesupport_c.cpython-310-x86_64-linux-gnu.so
/home/nav2-ws/install/dwb_msgs/share/dwb_msgs/msg/CriticScore.idl
/home/nav2-ws/install/dwb_msgs/share/dwb_msgs/msg/LocalPlanEvaluation.idl
/home/nav2-ws/install/dwb_msgs/share/dwb_msgs/msg/Trajectory2D.idl
/home/nav2-ws/install/dwb_msgs/share/dwb_msgs/msg/TrajectoryScore.idl
/home/nav2-ws/install/dwb_msgs/share/dwb_msgs/srv/DebugLocalPlan.idl
/home/nav2-ws/install/dwb_msgs/share/dwb_msgs/srv/GenerateTrajectory.idl
/home/nav2-ws/install/dwb_msgs/share/dwb_msgs/srv/GenerateTwists.idl
/home/nav2-ws/install/dwb_msgs/share/dwb_msgs/srv/GetCriticScore.idl
/home/nav2-ws/install/dwb_msgs/share/dwb_msgs/srv/ScoreTrajectory.idl
/home/nav2-ws/install/dwb_msgs/share/dwb_msgs/msg/CriticScore.msg
/home/nav2-ws/install/dwb_msgs/share/dwb_msgs/msg/LocalPlanEvaluation.msg
/home/nav2-ws/install/dwb_msgs/share/dwb_msgs/msg/Trajectory2D.msg
/home/nav2-ws/install/dwb_msgs/share/dwb_msgs/msg/TrajectoryScore.msg
/home/nav2-ws/install/dwb_msgs/share/dwb_msgs/srv/DebugLocalPlan.srv
/home/nav2-ws/install/dwb_msgs/share/dwb_msgs/srv/DebugLocalPlan_Request.msg
/home/nav2-ws/install/dwb_msgs/share/dwb_msgs/srv/DebugLocalPlan_Response.msg
/home/nav2-ws/install/dwb_msgs/share/dwb_msgs/srv/GenerateTrajectory.srv
/home/nav2-ws/install/dwb_msgs/share/dwb_msgs/srv/GenerateTrajectory_Request.msg
/home/nav2-ws/install/dwb_msgs/share/dwb_msgs/srv/GenerateTrajectory_Response.msg
/home/nav2-ws/install/dwb_msgs/share/dwb_msgs/srv/GenerateTwists.srv
/home/nav2-ws/install/dwb_msgs/share/dwb_msgs/srv/GenerateTwists_Request.msg
/home/nav2-ws/install/dwb_msgs/share/dwb_msgs/srv/GenerateTwists_Response.msg
/home/nav2-ws/install/dwb_msgs/share/dwb_msgs/srv/GetCriticScore.srv
/home/nav2-ws/install/dwb_msgs/share/dwb_msgs/srv/GetCriticScore_Request.msg
/home/nav2-ws/install/dwb_msgs/share/dwb_msgs/srv/GetCriticScore_Response.msg
/home/nav2-ws/install/dwb_msgs/share/dwb_msgs/srv/ScoreTrajectory.srv
/home/nav2-ws/install/dwb_msgs/share/dwb_msgs/srv/ScoreTrajectory_Request.msg
/home/nav2-ws/install/dwb_msgs/share/dwb_msgs/srv/ScoreTrajectory_Response.msg
/home/nav2-ws/install/dwb_msgs/share/ament_index/resource_index/package_run_dependencies/dwb_msgs
/home/nav2-ws/install/dwb_msgs/share/ament_index/resource_index/parent_prefix_path/dwb_msgs
/home/nav2-ws/install/dwb_msgs/share/dwb_msgs/environment/ament_prefix_path.sh
/home/nav2-ws/install/dwb_msgs/share/dwb_msgs/environment/ament_prefix_path.dsv
/home/nav2-ws/install/dwb_msgs/share/dwb_msgs/environment/path.sh
/home/nav2-ws/install/dwb_msgs/share/dwb_msgs/environment/path.dsv
/home/nav2-ws/install/dwb_msgs/share/dwb_msgs/local_setup.bash
/home/nav2-ws/install/dwb_msgs/share/dwb_msgs/local_setup.sh
/home/nav2-ws/install/dwb_msgs/share/dwb_msgs/local_setup.zsh
/home/nav2-ws/install/dwb_msgs/share/dwb_msgs/local_setup.dsv
/home/nav2-ws/install/dwb_msgs/share/dwb_msgs/package.dsv
/home/nav2-ws/install/dwb_msgs/share/ament_index/resource_index/packages/dwb_msgs
/home/nav2-ws/install/dwb_msgs/share/dwb_msgs/cmake/rosidl_cmake-extras.cmake
/home/nav2-ws/install/dwb_msgs/share/dwb_msgs/cmake/ament_cmake_export_dependencies-extras.cmake
/home/nav2-ws/install/dwb_msgs/share/dwb_msgs/cmake/ament_cmake_export_include_directories-extras.cmake
/home/nav2-ws/install/dwb_msgs/share/dwb_msgs/cmake/ament_cmake_export_libraries-extras.cmake
/home/nav2-ws/install/dwb_msgs/share/dwb_msgs/cmake/ament_cmake_export_targets-extras.cmake
/home/nav2-ws/install/dwb_msgs/share/dwb_msgs/cmake/rosidl_cmake_export_typesupport_targets-extras.cmake
/home/nav2-ws/install/dwb_msgs/share/dwb_msgs/cmake/rosidl_cmake_export_typesupport_libraries-extras.cmake
/home/nav2-ws/install/dwb_msgs/share/dwb_msgs/cmake/dwb_msgsConfig.cmake
/home/nav2-ws/install/dwb_msgs/share/dwb_msgs/cmake/dwb_msgsConfig-version.cmake
/home/nav2-ws/install/dwb_msgs/share/dwb_msgs/package.xml

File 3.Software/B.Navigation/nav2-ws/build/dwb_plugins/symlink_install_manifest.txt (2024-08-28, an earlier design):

/home/nav2-ws/install/dwb_plugins/lib/libstandard_traj_generator.so
/home/nav2-ws/install/dwb_plugins/include//dwb_plugins/kinematic_parameters.hpp
/home/nav2-ws/install/dwb_plugins/include//dwb_plugins/limited_accel_generator.hpp
/home/nav2-ws/install/dwb_plugins/include//dwb_plugins/one_d_velocity_iterator.hpp
/home/nav2-ws/install/dwb_plugins/include//dwb_plugins/standard_traj_generator.hpp
/home/nav2-ws/install/dwb_plugins/include//dwb_plugins/velocity_iterator.hpp
/home/nav2-ws/install/dwb_plugins/include//dwb_plugins/xy_theta_iterator.hpp
/home/nav2-ws/install/dwb_plugins/share/dwb_plugins/plugins.xml
/home/nav2-ws/install/dwb_plugins/share/dwb_plugins/environment/library_path.sh
/home/nav2-ws/install/dwb_plugins/share/dwb_plugins/environment/library_path.dsv
/home/nav2-ws/install/dwb_plugins/share/dwb_plugins//plugins.xml
/home/nav2-ws/install/dwb_plugins/share/ament_index/resource_index/package_run_dependencies/dwb_plugins
/home/nav2-ws/install/dwb_plugins/share/ament_index/resource_index/parent_prefix_path/dwb_plugins
/home/nav2-ws/install/dwb_plugins/share/dwb_plugins/environment/ament_prefix_path.sh
/home/nav2-ws/install/dwb_plugins/share/dwb_plugins/environment/ament_prefix_path.dsv
/home/nav2-ws/install/dwb_plugins/share/dwb_plugins/environment/path.sh
/home/nav2-ws/install/dwb_plugins/share/dwb_plugins/environment/path.dsv
/home/nav2-ws/install/dwb_plugins/share/dwb_plugins/local_setup.bash
/home/nav2-ws/install/dwb_plugins/share/dwb_plugins/local_setup.sh
/home/nav2-ws/install/dwb_plugins/share/dwb_plugins/local_setup.zsh
/home/nav2-ws/install/dwb_plugins/share/dwb_plugins/local_setup.dsv
/home/nav2-ws/install/dwb_plugins/share/dwb_plugins/package.dsv
/home/nav2-ws/install/dwb_plugins/share/ament_index/resource_index/packages/dwb_plugins
/home/nav2-ws/install/dwb_plugins/share/ament_index/resource_index/dwb_core__pluginlib__plugin/dwb_plugins
/home/nav2-ws/install/dwb_plugins/share/dwb_plugins/cmake/ament_cmake_export_include_directories-extras.cmake
/home/nav2-ws/install/dwb_plugins/share/dwb_plugins/cmake/ament_cmake_export_libraries-extras.cmake
/home/nav2-ws/install/dwb_plugins/share/dwb_plugins/cmake/dwb_pluginsConfig.cmake
/home/nav2-ws/install/dwb_plugins/share/dwb_plugins/cmake/dwb_pluginsConfig-version.cmake
/home/nav2-ws/install/dwb_plugins/share/dwb_plugins/package.xml

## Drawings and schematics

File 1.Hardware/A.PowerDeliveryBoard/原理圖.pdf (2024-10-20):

## POWER

## 12V接口

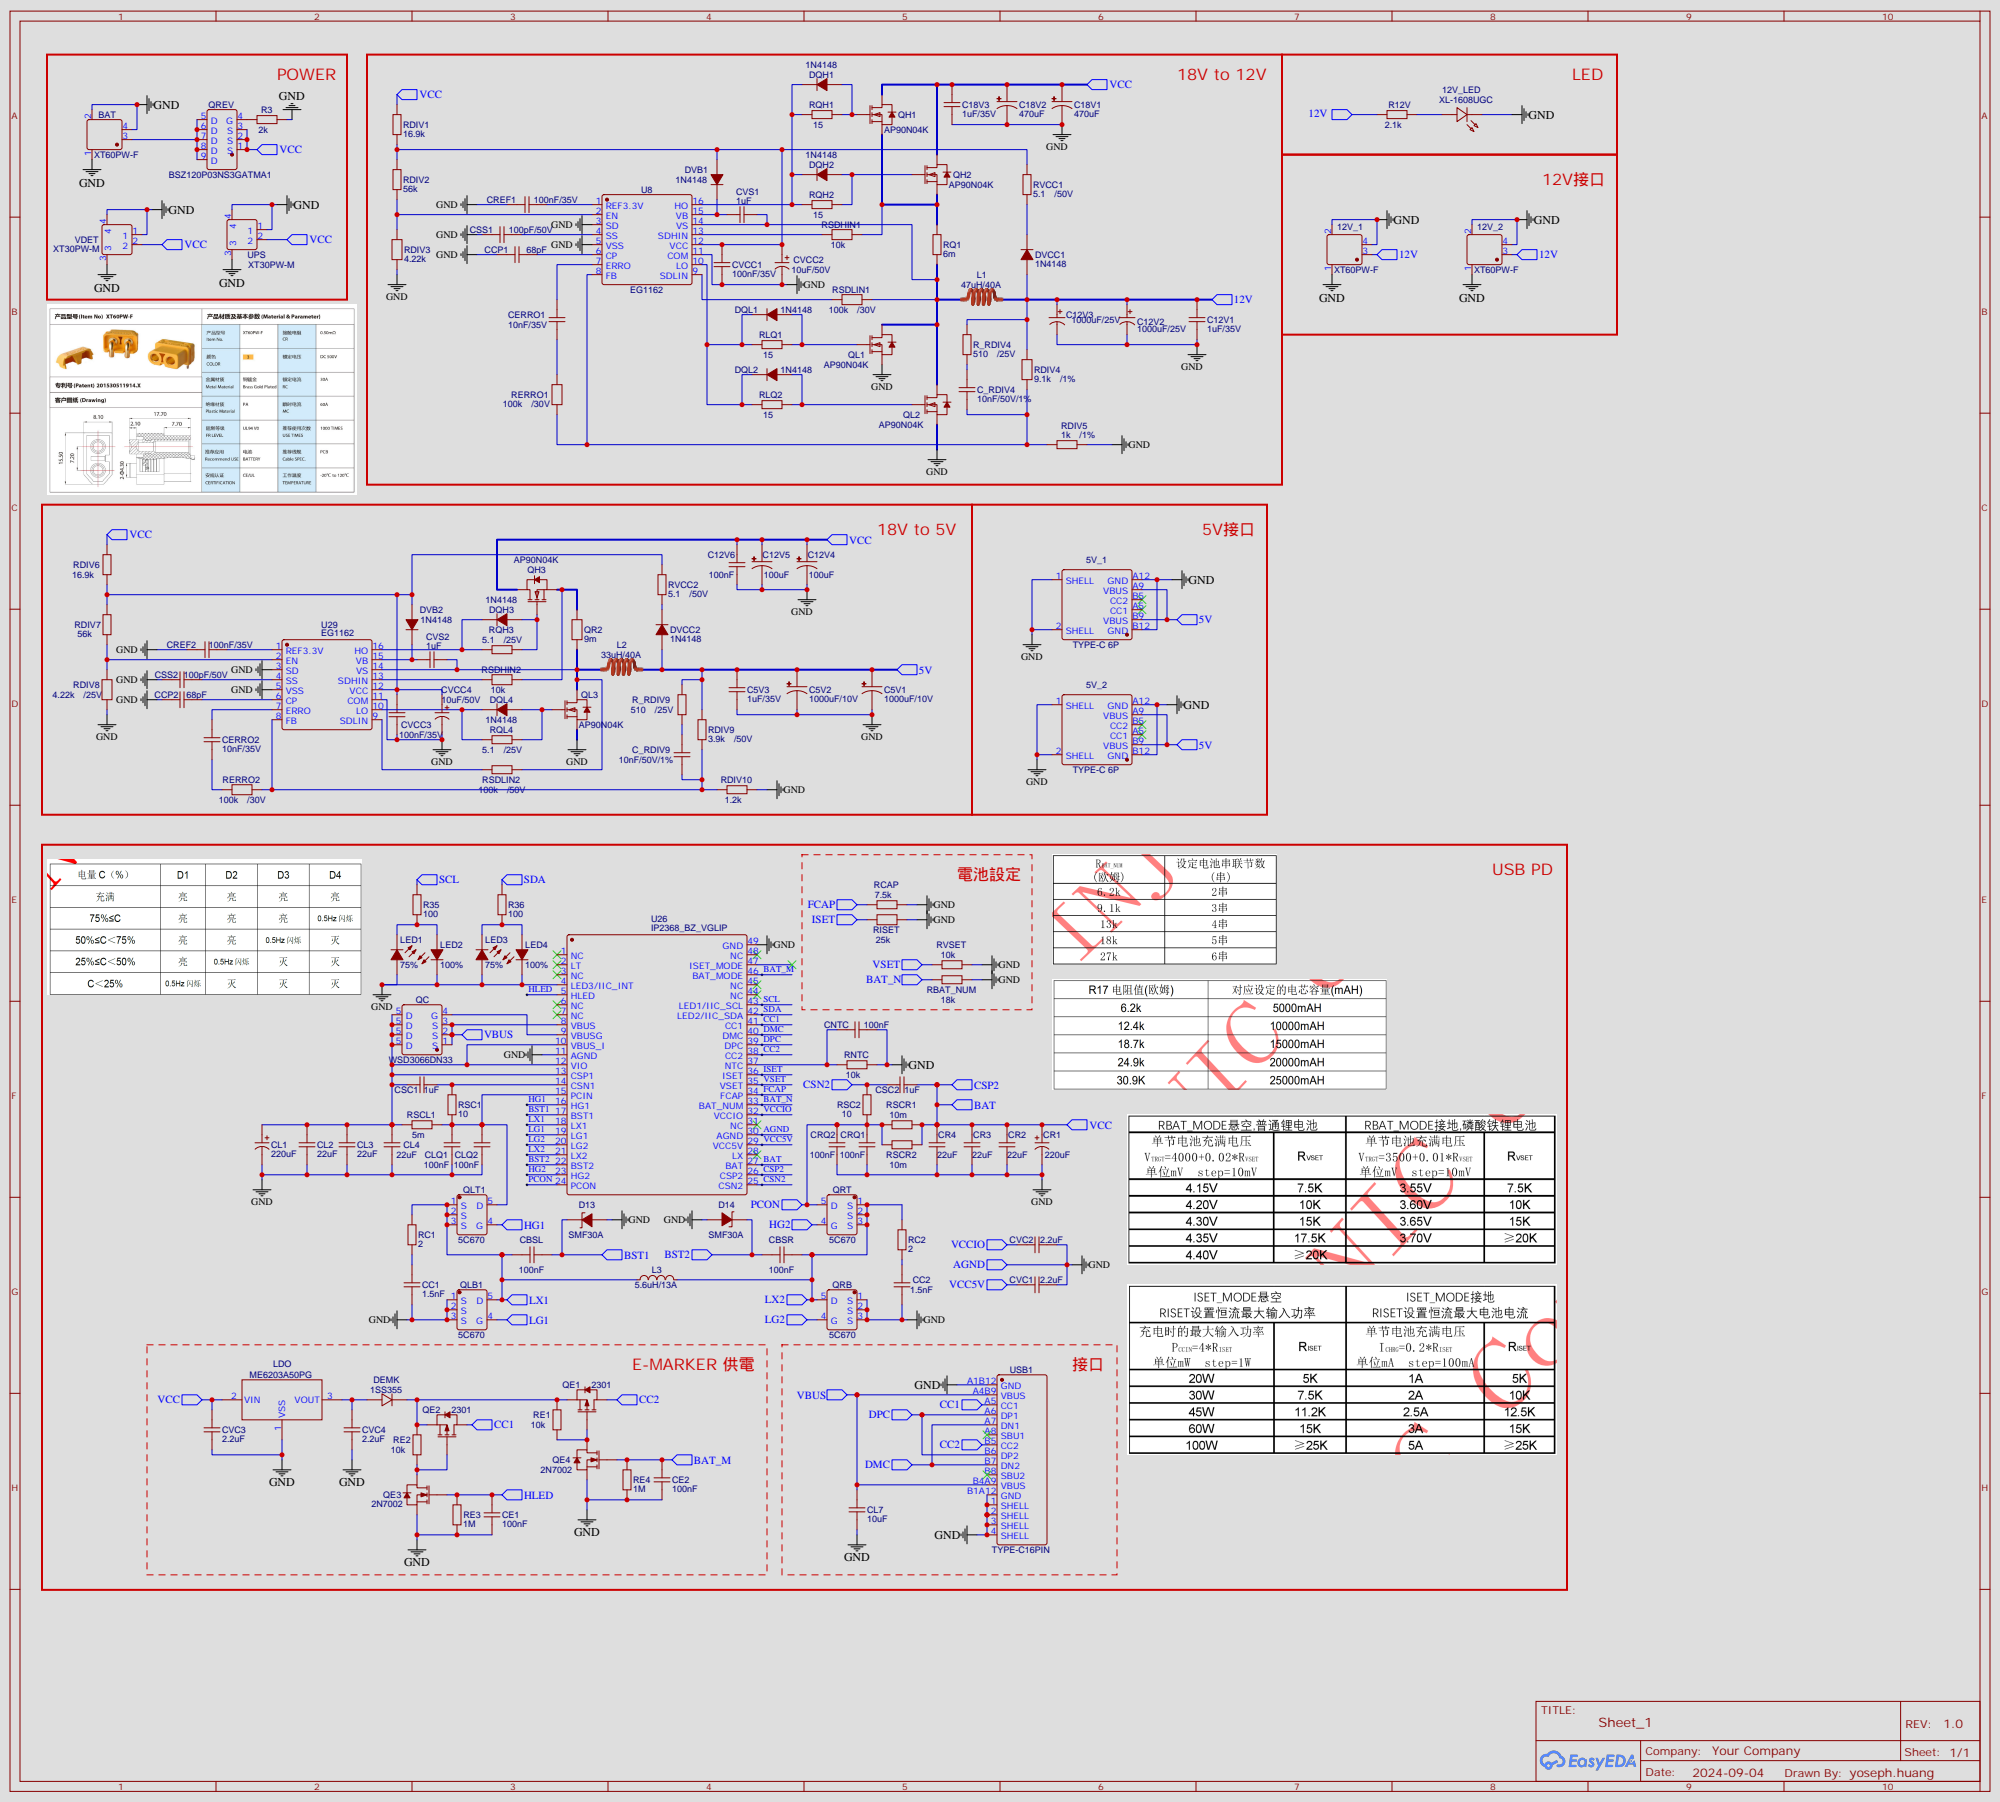
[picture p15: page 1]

LO 10 COM 11 VCC 12 SDHIN 13 VS 14 VB 15 HO 16

Drawn By: yoseph.huang

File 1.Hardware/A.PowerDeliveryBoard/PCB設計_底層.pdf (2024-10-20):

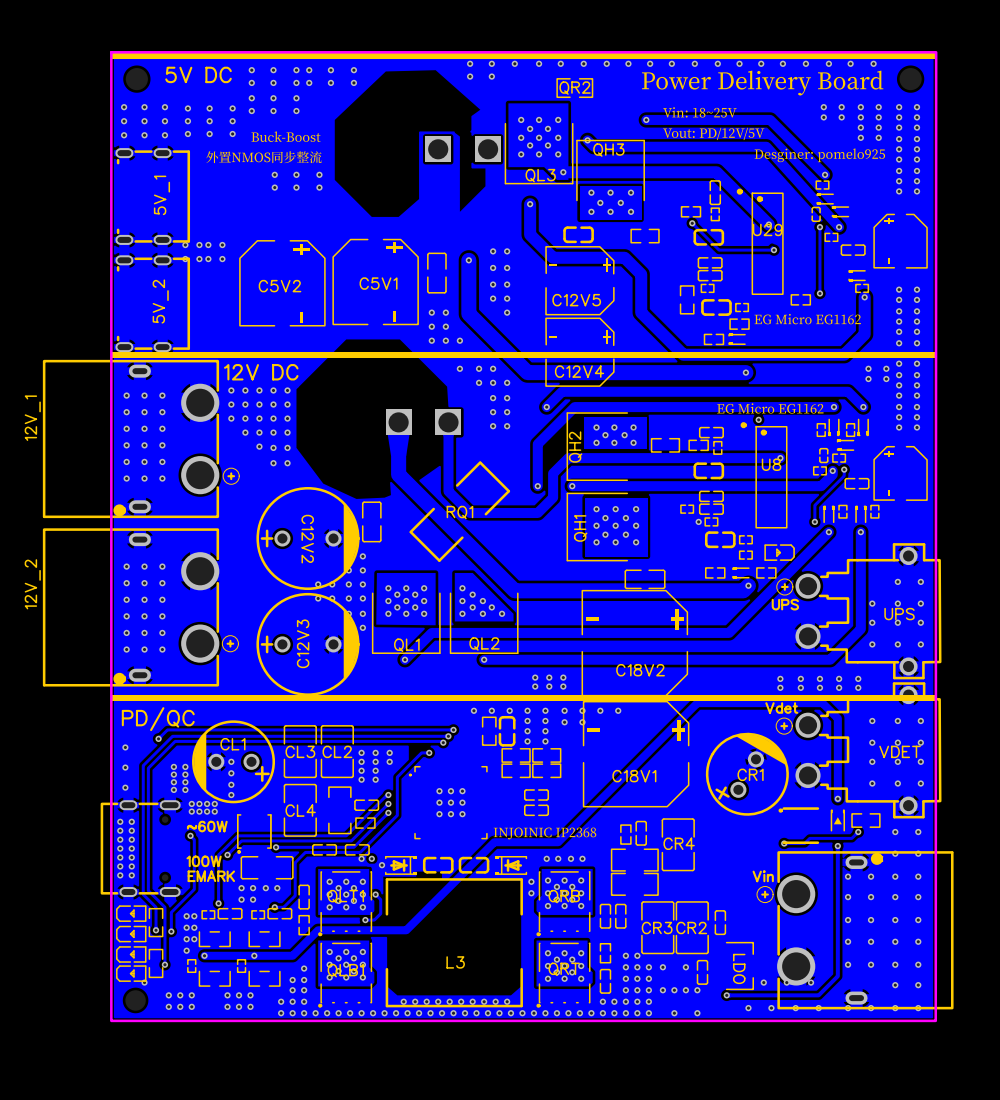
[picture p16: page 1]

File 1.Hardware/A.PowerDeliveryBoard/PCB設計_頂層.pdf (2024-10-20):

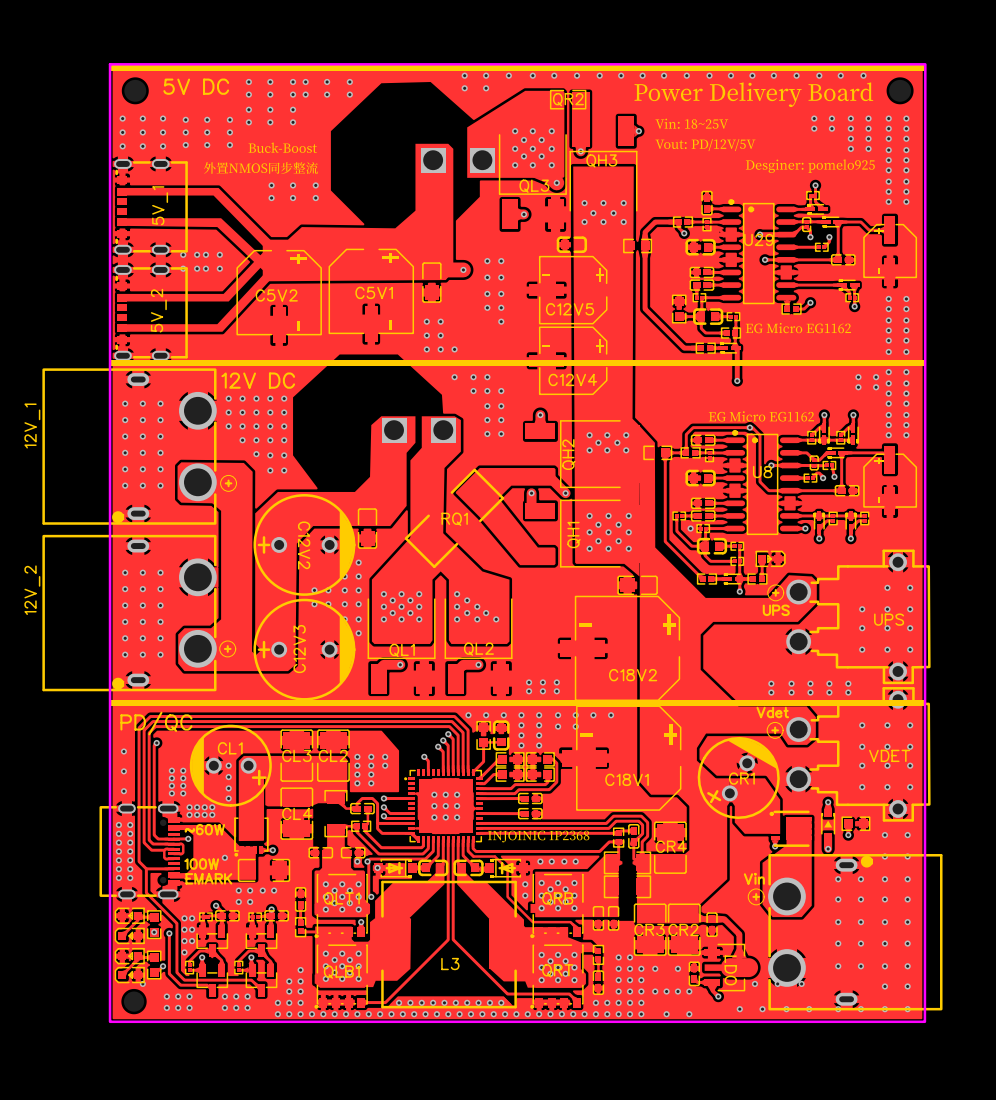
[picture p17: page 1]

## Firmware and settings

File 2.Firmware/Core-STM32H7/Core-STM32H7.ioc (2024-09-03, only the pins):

Mcu.UserName=STM32H723ZGTx
PA0.Signal=S_TIM5_CH1
PA1.Signal=S_TIM5_CH2
PA10.Signal=USART1_RX
PA15(JTDI).Signal=S_TIM2_CH1_ETR
PA6.Signal=S_TIM3_CH1
PA7.Signal=S_TIM3_CH2
PA9.Signal=USART1_TX
PB3(JTDO/TRACESWO).Signal=S_TIM2_CH2
PC6.Signal=S_TIM8_CH1
PC7.Signal=S_TIM8_CH2
PD0.Signal=GPIO_Output
PD1.Signal=GPIO_Output
PD12.Signal=S_TIM4_CH1
PD13.Signal=S_TIM4_CH2
PD2.Signal=GPIO_Output
PD3.Signal=GPIO_Output
PD4.Signal=GPIO_Output
PE11.Signal=S_TIM1_CH2
PE5.Signal=S_TIM15_CH1
PE6.Signal=S_TIM15_CH2
PE9.Signal=S_TIM1_CH1
PF0.Signal=TIM23_CH1
PF1.Signal=S_TIM23_CH2
PF11.Signal=TIM24_CH1
PF12.Signal=S_TIM24_CH2
PF2.Signal=S_TIM23_CH3
PG5.Signal=GPIO_Input
PG6.Signal=GPIO_Input
PG7.Signal=GPIO_Input
PG8.Signal=GPIO_Input
PH0-OSC_IN.Signal=RCC_OSC_IN
PH1-OSC_OUT.Signal=RCC_OSC_OUT

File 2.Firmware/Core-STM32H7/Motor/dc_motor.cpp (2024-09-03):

/*
 * motor.cpp
 *
 *  Created on: Aug 6, 2024
 *      Author: pomelo925
 */

#include "stm32h7xx_hal.h"

#include <dc_motor.h>

/** Timer **/
extern TIM_HandleTypeDef htim1;
extern TIM_HandleTypeDef htim3;
extern TIM_HandleTypeDef htim4;
extern TIM_HandleTypeDef htim5;
extern TIM_HandleTypeDef htim6;
extern TIM_HandleTypeDef htim8;
extern TIM_HandleTypeDef htim15;
extern TIM_HandleTypeDef htim23;
extern TIM_HandleTypeDef htim24;


/** Motors Instances**/
DC_MOTOR WheelRight(GPIOD, GPIO_PIN_3);
DC_MOTOR WheelLeft(GPIOD, GPIO_PIN_4);
// DC_MOTOR Intake;
// DC_MOTOR Elevator;


/**
 * @brief 馬達初始化
 * @param void
 */
void DC_MOTOR::init(void){  
  /* 啟動對應 Timer */
	HAL_TIM_Encoder_Start(&htim1, TIM_CHANNEL_ALL);
	HAL_TIM_Encoder_Start(&htim3, TIM_CHANNEL_ALL);
	HAL_TIM_Encoder_Start(&htim4, TIM_CHANNEL_ALL);
	HAL_TIM_Encoder_Start(&htim5, TIM_CHANNEL_ALL);
	HAL_TIM_Encoder_Start(&htim8, TIM_CHANNEL_ALL);
	HAL_TIM_Encoder_Start(&htim24, TIM_CHANNEL_ALL);


	HAL_TIM_Base_Start_IT(&htim6);

	HAL_TIM_PWM_Start_IT(&htim15, TIM_CHANNEL_1);
	HAL_TIM_PWM_Start_IT(&htim15, TIM_CHANNEL_2);
	HAL_TIM_PWM_Start_IT(&htim23, TIM_CHANNEL_1);
	HAL_TIM_PWM_Start_IT(&htim23, TIM_CHANNEL_2);
	HAL_TIM_PWM_Start_IT(&htim23, TIM_CHANNEL_3);

  // 初始化各個電機的參數
  WheelRight.setPID(2.5f, 80.f, 0.f);
  WheelRight.setInfo(1024.f, 26.f, 0.001f);
  WheelRight.setInverse(true);

  WheelLeft.setPID(2.5f, 80.f, 0.f);
  WheelLeft.setInfo(1024.f, 26.f, 0.001f);
  WheelLeft.setInverse(true);

  // Intake.setPID(2.5f, 100.f, 0.f);
  // Intake.setInfo(512.f, 20.8f, 0.001f);
  // Intake.setInverse(false);

  // Elevator.setPID(2.5f, 100.f, 0.f);
  // Elevator.setInfo(512.f, 20.8f, 0.001f);
  // Elevator.setInverse(false);

  return;
}


/**
 * @brief 更新當前輪速 (rad/s)
 */
void DC_MOTOR::updateCurrentSpeed(const int16_t currentPulse) {
  _current_pulse = currentPulse;
  float speed = (float)(_current_pulse / 4 / _encoder_res / _sr_ratio / _interval) * 2.f * M_PI;
  _current_wheel_speed = _is_inverse ? speed : -speed;
  return;
}


/**
 * @brief 更新目標 PWM 輸出
 * @param void
 */
void DC_MOTOR::updateTargetPWM(void) {
  _error = _target_wheel_speed - _current_wheel_speed;
  _integral += (_error * _interval);

  // 防止積分飽和
  if (_target_wheel_speed == 0) {
    _integral = 0;
  } else {
    _integral = std::clamp(_integral, -MAX_INTEGRAL / _ki, MAX_INTEGRAL / _ki);
  }

  float derivative = (_error - _previous_error) / _interval;
  _previous_error = _error;

  // 計算 PID 輸出
  _target_PWM = _error * _kp + _integral * _ki + derivative * _kd;

  // 限制 PWM 輸出
  _target_PWM = std::clamp(_target_PWM, -MAX_PWM, MAX_PWM);
  
  // 更新方向
  _is_positive_direction = (_target_PWM >= 0);
  
  return;
}


/**
 * @brief 取得當前輪速 (rad/s)
 * @param void
 * @return 當前輪速 (rad)
 */
float DC_MOTOR::get_current_wheel_speed(void) const {
  return _current_wheel_speed;
}


/**
 * @brief 取得 PWM 目標輸出
 * @param void
 * @return PWM 目標輸出
 */
float DC_MOTOR::get_target_pwm(void) const {
  return _target_PWM;
};


/**
 * @brief 設定目標輪速 (rad/s)
 * @param speed 目標輪速
 */
void DC_MOTOR::set_target_wheel_speed(float speed){
  _target_wheel_speed = speed;
  return;
};


/**
 * @brief 設置PID參數
 * @param kp P參數
 * @param ki I參數
 * @param kd D參數
 */
void DC_MOTOR::setPID(float kp, float ki, float kd) {
  _kp = kp;
  _ki = ki;
  _kd = kd;
}


/**
 * @brief 設置電機訊息
 * @param encoder_res 編碼器分辨率
 * @param sr_ratio 齒輪比
 * @param interval 時間間隔
 */
void DC_MOTOR::setInfo(float encoder_res, float sr_ratio, float interval) {
  _encoder_res = encoder_res;
  _sr_ratio = sr_ratio;
  _interval = interval;
}


/**
 * @brief 設置電機旋轉方向
 * @param is_inverse 是否反向旋轉
 */
void DC_MOTOR::setInverse(bool is_inverse){
  _is_inverse = is_inverse;
  return;
}


/**
 * @brief 更新當前輪速 (rad/s) 和目標 PWM
 * @param currentCount 當前脈波數
 */
void DC_MOTOR::update(int16_t currentCount) {
  updateCurrentSpeed(currentCount);
  updateTargetPWM();
  return;
}


/**
 * @brief 取得電機旋轉方向
 * @param void
 * @return 電機旋轉方向
 */
GPIO_PinState DC_MOTOR::getDirection(void) const {
  bool actual_direction = _is_positive_direction;
  if (_is_inverse) actual_direction = !actual_direction;
  return actual_direction ? GPIO_PIN_SET : GPIO_PIN_RESET;
}


/**
 * @brief 取得 PWM 值
 * @param void
 * @return PWM 值
 */
uint32_t DC_MOTOR::getPWMValue(void) const {
  return static_cast<uint32_t>(fabs(_target_PWM));
}

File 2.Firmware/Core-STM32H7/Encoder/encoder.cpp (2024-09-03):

/*
 * motor.cpp
 *
 *  Created on: Aug 27, 2024
 *      Author: renee0630
 */

#include "../Encoder/encoder.h"

#include "stm32h7xx_hal.h"


/** Timer **/
extern TIM_HandleTypeDef htim1;
extern TIM_HandleTypeDef htim3;

/** Encoder Instances**/
ENCODER EncoderRight;
ENCODER EncoderLeft;


/**
 * @brief 編碼器初始化
 * @param void
 */
void ENCODER::init(void){
  /* 啟動對應 Timer */
	HAL_TIM_Encoder_Start(&htim1, TIM_CHANNEL_ALL);
	HAL_TIM_Encoder_Start(&htim3, TIM_CHANNEL_ALL);


  // 初始化各個編碼器的參數
  EncoderRight.setInfo(1000.f, 1.f, 0.001f);
  EncoderRight.setInverse(true);

  EncoderLeft.setInfo(1000.f, 1.f, 0.001f);
  EncoderLeft.setInverse(true);

  return;
}


/**
 * @brief 更新當前輪速 (rad/s)
 */
void ENCODER::updateCurrentSpeed(const int16_t currentPulse) {
  _current_pulse = currentPulse;
  float speed = (_current_pulse / 4 / 1000.f / 1.f / 0.001f) * 2.f * M_PI;
  _current_wheel_speed = _is_inverse ? speed : -speed;
  return;
}


/**
 * @brief 取得當前輪速 (rad/s)
 * @param void
 * @return 當前輪速 (rad)
 */
float ENCODER::get_current_wheel_speed(void) const {
  return _current_wheel_speed;
}


/**
 * @brief 設置電機訊息
 * @param encoder_res 編碼器分辨率
 * @param sr_ratio 齒輪比
 * @param interval 時間間隔
 */
void ENCODER::setInfo(float encoder_res, float sr_ratio, float interval) {
  _encoder_res = encoder_res;
  _sr_ratio = sr_ratio;
  _interval = interval;
}


/**
 * @brief 設置電機旋轉方向
 * @param is_inverse 是否反向旋轉
 */
void ENCODER::setInverse(bool is_inverse){
  _is_inverse = is_inverse;
  return;
}


/**
 * @brief 更新當前輪速 (rad/s)
 * @param currentCount 當前脈波數
 */
void ENCODER::update(int16_t currentCount) {
  updateCurrentSpeed(currentCount);
  return;
}

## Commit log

2024-04-11 add tx2 model
    [032-0037-000_2.ipt, 032-0056-000_2.ipt, 032-0131-000_2.ipt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]
2024-04-18 epomaker rt100 container
    [epomaker_RT100.ipt, epomaker_RT100.stl]
2024-04-19 update rt100
    [epomaker_RT100.ipt, epomaker_RT100.stl]
2024-06-10 rtabmap env created
    [032-0037-000_2.ipt, 032-0056-000_2.ipt, 032-0131-000_2.ipt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]
2024-07-06 navigation architecture established #2
    [turtlebot3_waffle.urdf]
2024-07-14 rtabmap ros2 arch confirmed #1
    [turtlebot3_waffle.urdf]
2024-07-15 navigation exploration-mode built #2
    [turtlebot3_waffle.urdf]
2024-07-24 sercices subpages framework build up
2024-08-03 rtabmap multi-stage dockerfile
2024-08-03 nav2 arch confirmed #2
    [KinematicParams.cfg, common_properties.urdf, model-1_4.sdf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]
2024-08-07 stm32 pid control first edition
2024-08-11 complete : stm32 architecture & ros communication
2024-08-11 optimization: dc motor structure
2024-08-20 edgenn on-device programming testing pass
2024-08-28 nav2 binary files
    [turtlebot3_waffle.urdf]
2024-08-29 add nav2 source code
    [common_properties.urdf, model-1_4.sdf, model.sdf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]
2024-09-03 add PID control
2024-10-20 PCB: add power delivery board
    [PCB走線.pcbdoc, 原理圖.schdoc]
2024-10-24 chassis new
